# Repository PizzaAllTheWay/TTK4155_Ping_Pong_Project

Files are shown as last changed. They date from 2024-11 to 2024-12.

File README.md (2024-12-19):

# Ping Pong Project
A School project for subject TTK4155. The goal of the project is to teach students how to develop and design Embedded Systems

Lord Have mercy on us
Let the grind BEGIN!

# Demo Video
Demo Video (https://www.youtube.com/watch?v=QTJpXrNRjtw)

Raw link: https://www.youtube.com/watch?v=QTJpXrNRjtw

# PCB
Very cool, very clean, thank you Benjamin for making an awesome PCB <3

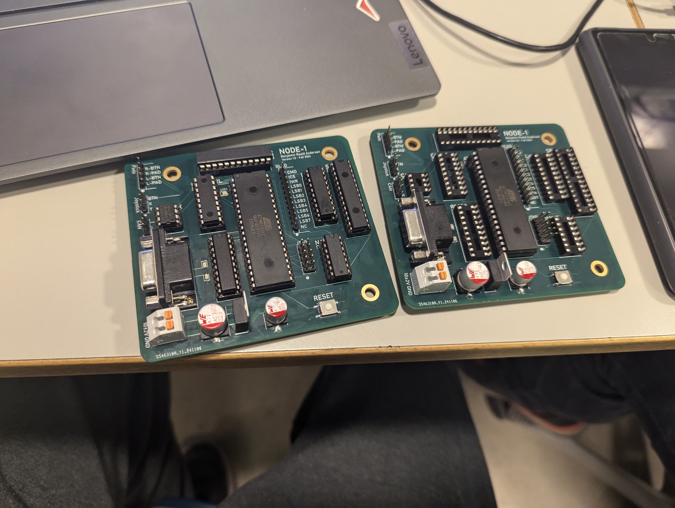
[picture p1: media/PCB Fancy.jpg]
PCB Fancy


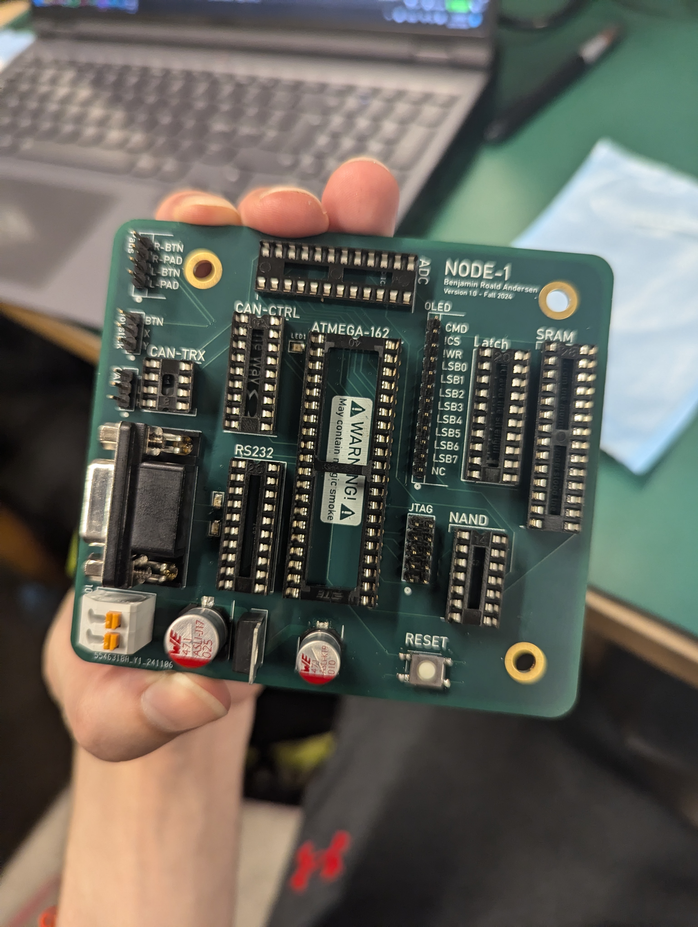
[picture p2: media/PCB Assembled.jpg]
PCB Assembled


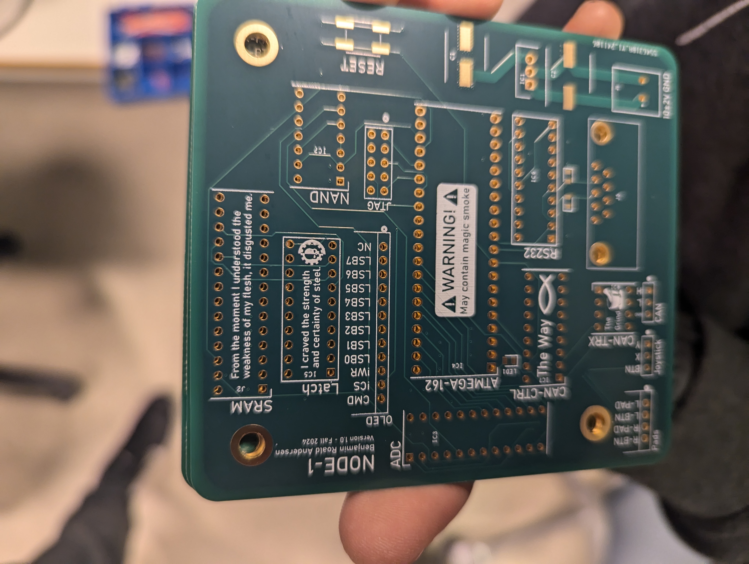
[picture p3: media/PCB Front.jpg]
PCB Front

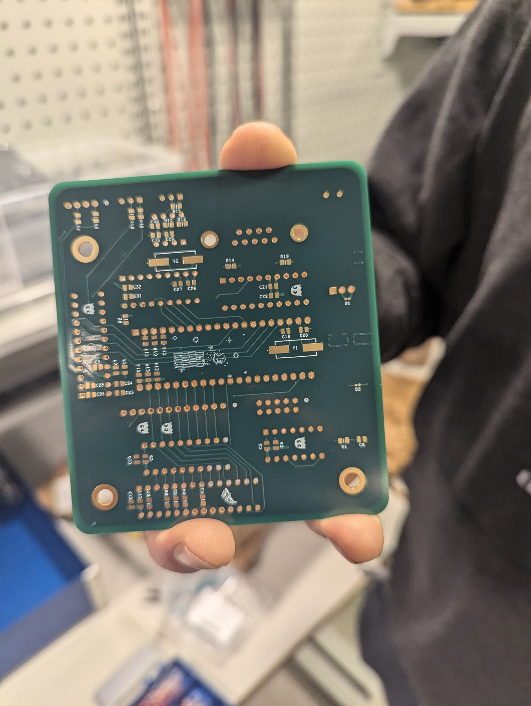
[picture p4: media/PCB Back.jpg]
PCB Back


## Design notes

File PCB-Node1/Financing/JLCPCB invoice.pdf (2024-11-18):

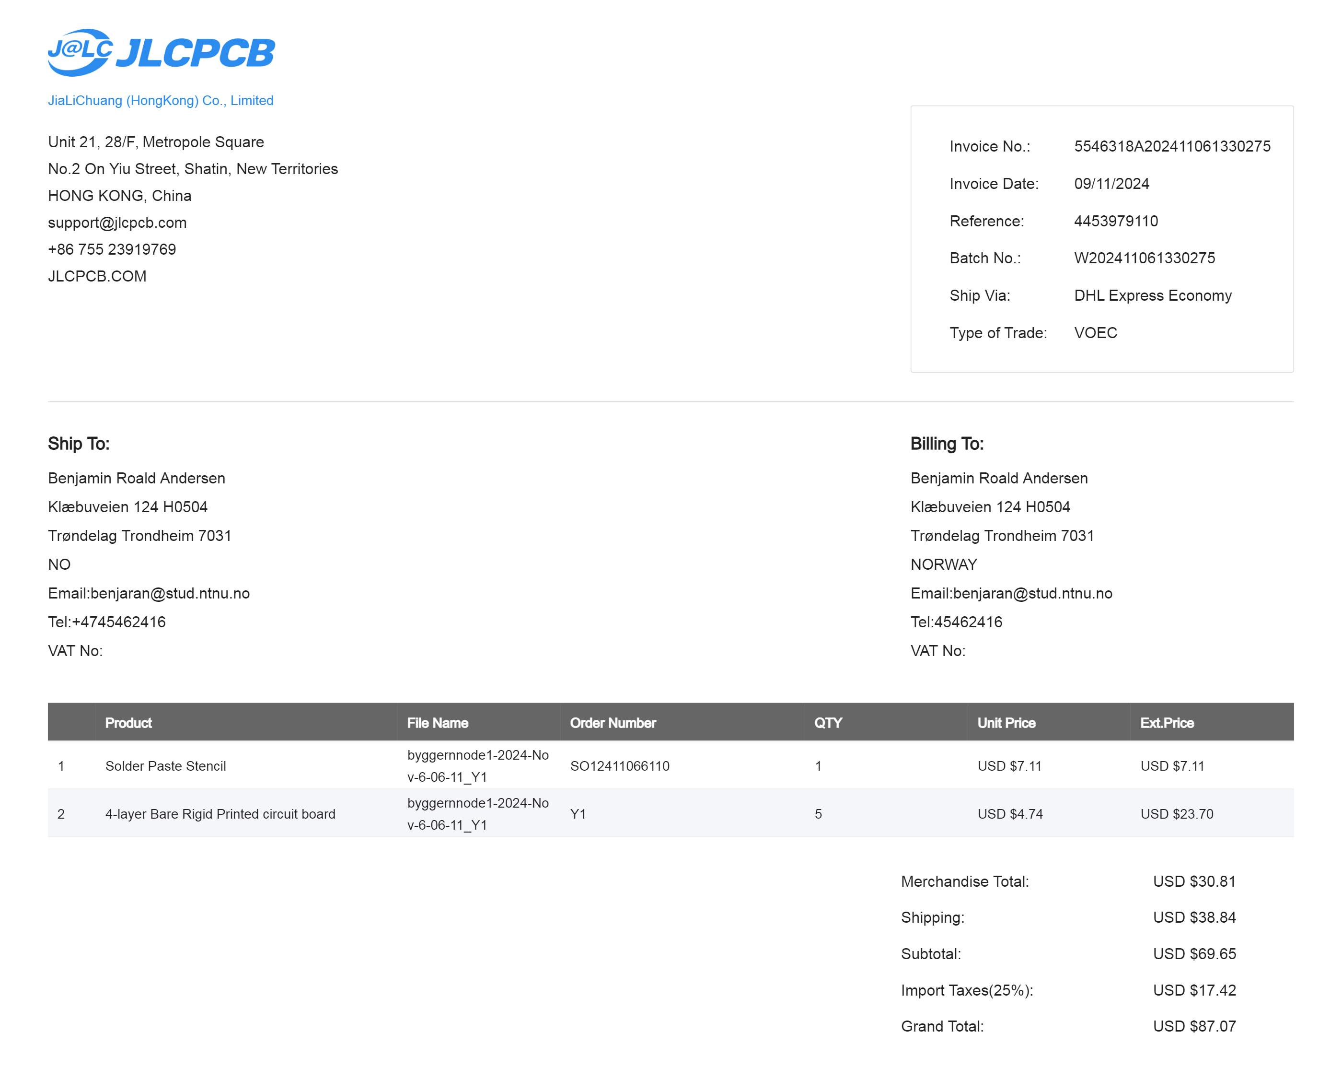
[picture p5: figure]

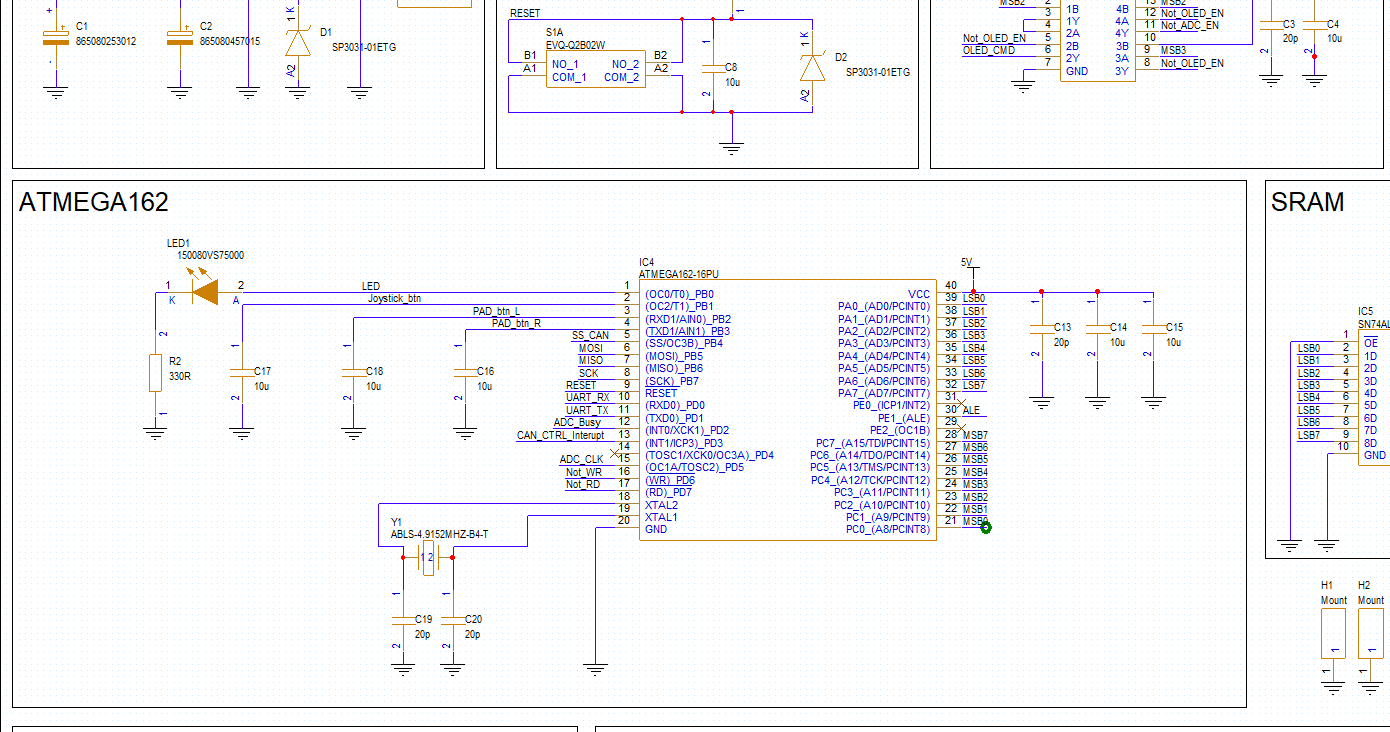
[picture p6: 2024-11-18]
PCB-Node1/Project/byggernnode1/BYGGERNNODE1.png

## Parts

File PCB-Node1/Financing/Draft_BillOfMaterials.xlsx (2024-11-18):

Connectors
3pinheader
amount per board | Capasitors | name | use | link | individual cost | Total cost
1 | 865080457015 | HV 470u | Filter | https://www.digikey.no/no/products/detail/w%C3%BCrth-elektronik/865080457015/5728038
1 | 865080253012 | 470u | Filter | https://www.digikey.no/no/products/detail/w%C3%BCrth-elektronik/865080253012/5728090
 | 885012107010 | 10u | decoupling | https://www.digikey.no/no/products/detail/w%C3%BCrth-elektronik/885012107010/5453475
2 | CC0805JRNPO9BN180 | 18p | OSC cap | https://www.digikey.no/no/products/detail/yageo/CC0805JRNPO9BN180/302836
2 | CC0805JRNPO9BN200 | 20p | OSC cap
 | 885012207098 | 100n | Filter | https://www.digikey.no/no/products/detail/w%C3%BCrth-elektronik/885012207098/5453935
 | Resistor
 | ERJ-6GEYJ103V | 10k |  | https://www.digikey.no/no/products/detail/panasonic-electronic-components/ERJ-6GEYJ103V/83062
 | ERJ-6GEYJ331V | 330R |  | https://www.digikey.no/no/products/detail/panasonic-electronic-components/ERJ-6GEYJ331V/89726
 | ERJ-6GEYJ202V | 2k |  | https://www.digikey.no/no/products/detail/panasonic-electronic-components/ERJ-6GEYJ202V/83028
 | Crystal
1 | ECS-160-20-5PX-TR |  | Can OSC | https://www.digikey.no/no/products/detail/ecs-inc/ECS-160-20-5PX-TR/765265
1 | ABLS-4.9152MHZ-B4-T |  | AT162 OSC | https://www.digikey.no/no/products/detail/abracon-llc/ABLS-4-9152MHZ-B4-T/2184149
 | LED
3 | 150080VS75000 | green LED | debug | https://www.digikey.no/no/products/detail/w%C3%BCrth-elektronik/150080VS75000/4489924
 | Button
1 | EVQ-Q2B02W |  |  | https://www.digikey.no/no/products/detail/panasonic-electronic-components/EVQ-Q2B02W/762881
 | Ssockets
1 | ED281DT |  | SRAM | https://www.digikey.no/no/products/detail/on-shore-technology-inc/ED281DT/4147600
1 | 1-2199299-5 |  | ATMEGA162 | https://www.digikey.no/no/products/detail/te-connectivity-amp-connectors/1-2199299-5/5022052
1 | DILB24P-224TLF |  | ADC | https://www.digikey.no/no/products/detail/amphenol-cs-fci/DILB24P-224TLF/5204412
1 | DILB14P-223TLF |  | NAND | https://www.digikey.no/no/products/detail/amphenol-cs-fci/DILB14P-223TLF/4292071
1 | DILB16P-223TLF |  | RS232 | https://www.digikey.no/no/products/detail/amphenol-cs-fci/DILB16P-223TLF/4292068
1 | DILB18P-223TLF |  | CAN ctrl | https://www.digikey.no/no/products/detail/amphenol-cs-fci/DILB18P-223TLF/5204410
1 | DILB8P-223TLF |  | CAN transceiver | https://www.digikey.no/no/products/detail/amphenol-cs-fci/DILB8P-223TLF/4292069
1 | DILB20P-223TLF |  | Adress latch | https://www.digikey.no/no/products/detail/amphenol-cs-fci/DILB20P-223TLF/4292067
 | 1 row Header pins
1 | 61302211121 |  | pinheader 1 row | https://www.digikey.no/no/products/detail/w%C3%BCrth-elektronik/61302211121/4846864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
 | 2 row header pins
1 | 61301021121 |  | Jtag 2 row | https://www.digikey.no/no/products/detail/w%C3%BCrth-elektronik/61301021121/2508441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

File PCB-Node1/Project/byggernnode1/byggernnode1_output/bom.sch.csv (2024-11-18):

Item Number | Quantity | Value | Description | Part Number | Part Reference | Manufacturer Name | Manufacturer Part Number | ID | SKU
1 | 1 | 865080253012 | Wurth Elektronik 470uF 10 V dc Aluminium Electrolytic Capacitor, WCAP-ASLI Series 2000h 8 (Dia.) x 10.35mm | 865080253012 | C1 | Würth Elektronik | 865080253012 | 440
2 | 1 | 865080457015 | Wurth Elektronik 470uF 25 V dc Aluminium Electrolytic Capacitor, WCAP-ASLI Series 2000h 10 (Dia.) x 10.35mm | 865080457015 | C2 | Würth Elektronik | 865080457015 | 437
3 | 1 | 20p | Multilayer Ceramic Chip Capacitor WCAP-CSGP Series 0805 10000000pF X5R0805106M010DFCT10000 | 885012107010 | C3 | Würth Elektronik | 885012107010 | 671
4 | 1 | 10u | Multilayer Ceramic Chip Capacitor WCAP-CSGP Series 0805 10000000pF X5R0805106M010DFCT10000 | 885012107010 | C4 | Würth Elektronik | 885012107010 | 674
5 | 1 | 10u | Multilayer Ceramic Chip Capacitor WCAP-CSGP Series 0805 10000000pF X5R0805106M010DFCT10000 | 885012107010 | C5 | Würth Elektronik | 885012107010 | 453
6 | 1 | 10u | Multilayer Ceramic Chip Capacitor WCAP-CSGP Series 0805 10000000pF X5R0805106M010DFCT10000 | 885012107010 | C6 | Würth Elektronik | 885012107010 | 456
7 | 1 | 20p | Multilayer Ceramic Chip Capacitor WCAP-CSGP Series 0805 10000000pF X5R0805106M010DFCT10000 | 885012107010 | C7 | Würth Elektronik | 885012107010 | 677
8 | 1 | 10u | Multilayer Ceramic Chip Capacitor WCAP-CSGP Series 0805 10000000pF X5R0805106M010DFCT10000 | 885012107010 | C8 | Würth Elektronik | 885012107010 | 521
9 | 1 | 20p | Multilayer Ceramic Chip Capacitor WCAP-CSGP Series 0805 10000000pF X5R0805106M010DFCT10000 | 885012107010 | C9 | Würth Elektronik | 885012107010 | 916
10 | 1 | 10u | Multilayer Ceramic Chip Capacitor WCAP-CSGP Series 0805 10000000pF X5R0805106M010DFCT10000 | 885012107010 | C10 | Würth Elektronik | 885012107010 | 919
11 | 1 | 20p | Multilayer Ceramic Chip Capacitor WCAP-CSGP Series 0805 10000000pF X5R0805106M010DFCT10000 | 885012107010 | C11 | Würth Elektronik | 885012107010 | 913
12 | 1 | 10u | Multilayer Ceramic Chip Capacitor WCAP-CSGP Series 0805 10000000pF X5R0805106M010DFCT10000 | 885012107010 | C12 | Würth Elektronik | 885012107010 | 910
13 | 1 | 20p | Multilayer Ceramic Chip Capacitor WCAP-CSGP Series 0805 10000000pF X5R0805106M010DFCT10000 | 885012107010 | C13 | Würth Elektronik | 885012107010 | 662
14 | 1 | 10u | Multilayer Ceramic Chip Capacitor WCAP-CSGP Series 0805 10000000pF X5R0805106M010DFCT10000 | 885012107010 | C14 | Würth Elektronik | 885012107010 | 665
15 | 1 | 10u | Multilayer Ceramic Chip Capacitor WCAP-CSGP Series 0805 10000000pF X5R0805106M010DFCT10000 | 885012107010 | C15 | Würth Elektronik | 885012107010 | 668
16 | 1 | 10u | Multilayer Ceramic Chip Capacitor WCAP-CSGP Series 0805 10000000pF X5R0805106M010DFCT10000 | 885012107010 | C16 | Würth Elektronik | 885012107010 | 450
17 | 1 | 10u | Multilayer Ceramic Chip Capacitor WCAP-CSGP Series 0805 10000000pF X5R0805106M010DFCT10000 | 885012107010 | C17 | Würth Elektronik | 885012107010 | 444
18 | 1 | 10u | Multilayer Ceramic Chip Capacitor WCAP-CSGP Series 0805 10000000pF X5R0805106M010DFCT10000 | 885012107010 | C18 | Würth Elektronik | 885012107010 | 447
19 | 1 | 20p | Multilayer Ceramic Chip Capacitor WCAP-CSGP Series 0805 10000000pF X5R0805106M010DFCT10000 | 885012107010 | C19 | Würth Elektronik | 885012107010 | 494
20 | 1 | 20p | Multilayer Ceramic Chip Capacitor WCAP-CSGP Series 0805 10000000pF X5R0805106M010DFCT10000 | 885012107010 | C20 | Würth Elektronik | 885012107010 | 491
21 | 1 | 20p | Multilayer Ceramic Chip Capacitor WCAP-CSGP Series 0805 10000000pF X5R0805106M010DFCT10000 | 885012107010 | C21 | Würth Elektronik | 885012107010 | 557
22 | 1 | 10u | Multilayer Ceramic Chip Capacitor WCAP-CSGP Series 0805 10000000pF X5R0805106M010DFCT10000 | 885012107010 | C22 | Würth Elektronik | 885012107010 | 553
23 | 1 | 100n | Multilayer Ceramic Chip Capacitor WCAP-CSGP Series 0805 10000000pF X5R0805106M010DFCT10000 | 885012107010 | C23 | Würth Elektronik | 885012107010 | 797
24 | 1 | 100n | Multilayer Ceramic Chip Capacitor WCAP-CSGP Series 0805 10000000pF X5R0805106M010DFCT10000 | 885012107010 | C24 | Würth Elektronik | 885012107010 | 801
25 | 1 | 10u | Multilayer Ceramic Chip Capacitor WCAP-CSGP Series 0805 10000000pF X5R0805106M010DFCT10000 | 885012107010 | C25 | Würth Elektronik | 885012107010 | 716
26 | 1 | 10u | Multilayer Ceramic Chip Capacitor WCAP-CSGP Series 0805 10000000pF X5R0805106M010DFCT10000 | 885012107010 | C26 | Würth Elektronik | 885012107010 | 713
27 | 1 | 20p | Multilayer Ceramic Chip Capacitor WCAP-CSGP Series 0805 10000000pF X5R0805106M010DFCT10000 | 885012107010 | C27 | Würth Elektronik | 885012107010 | 483
28 | 1 | 20p | Multilayer Ceramic Chip Capacitor WCAP-CSGP Series 0805 10000000pF X5R0805106M010DFCT10000 | 885012107010 | C28 | Würth Elektronik | 885012107010 | 486
29 | 1 | 20p | Multilayer Ceramic Chip Capacitor WCAP-CSGP Series 0805 10000000pF X5R0805106M010DFCT10000 | 885012107010 | C29 | Würth Elektronik | 885012107010 | 657
30 | 1 | 10u | Multilayer Ceramic Chip Capacitor WCAP-CSGP Series 0805 10000000pF X5R0805106M010DFCT10000 | 885012107010 | C30 | Würth Elektronik | 885012107010 | 654
31 | 1 | 20p | Multilayer Ceramic Chip Capacitor WCAP-CSGP Series 0805 10000000pF X5R0805106M010DFCT10000 | 885012107010 | C31 | Würth Elektronik | 885012107010 | 943
32 | 1 | 10u | Multilayer Ceramic Chip Capacitor WCAP-CSGP Series 0805 10000000pF X5R0805106M010DFCT10000 | 885012107010 | C32 | Würth Elektronik | 885012107010 | 940
33 | 1 | 10u | Multilayer Ceramic Chip Capacitor WCAP-CSGP Series 0805 10000000pF X5R0805106M010DFCT10000 | 885012107010 | C33 | Würth Elektronik | 885012107010 | 946
34 | 1 | CONN_003P_000C_1 |  | M20-9990345 | CAN_CONN1 | Harwin | M20-9990345 | 809
35 | 1 | SP3031-01ETG | ESD Suppressors / TVS Diodes 5V 1uA 10kV UNIDIRECTIONAL | SP3031-01ETG | D1 | LITTELFUSE | SP3031-01ETG | 1165
36 | 1 | SP3031-01ETG | ESD Suppressors / TVS Diodes 5V 1uA 10kV UNIDIRECTIONAL | SP3031-01ETG | D2 | LITTELFUSE | SP3031-01ETG | 1162
37 | 1 | Mount | Standoffs & Spacers WA-SMST SMT Steel 3.3mm Intrnl NonStop | 9774015960R | H1 | Würth Elektronik | 9774015960R | 949
38 | 1 | Mount | Standoffs & Spacers WA-SMST SMT Steel 3.3mm Intrnl NonStop | 9774015960R | H2 | Würth Elektronik | 9774015960R | 951
39 | 1 | Mount | Standoffs & Spacers WA-SMST SMT Steel 3.3mm Intrnl NonStop | 9774015960R | H3 | Würth Elektronik | 9774015960R | 953
40 | 1 | MC7805ACTG | 1A, 5V, Positive V Reg, MC7805ACTG MC7805ACTG, Voltage Regulator, 2.2A 5 V, +/-4%, 3-Pin TO-220 | MC7805ACTG | IC1 | onsemi | MC7805ACTG | 425
41 | 1 | SN74HC00N | Quad 2i/p NANDgate,SN74HC00N DIP14 25pcs | SN74HC00N | IC2 | Texas Instruments | SN74HC00N | 115
42 | 1 | MAX156BCNG+ | Analog to Digital Converters - ADC High-Speed, 8-Channel, 8-Bit ADC with Simultaneous Track/Holds and Reference | MAX156BCNG+ | IC3 | Analog Devices | MAX156BCNG+ | 86
43 | 1 | ATMEGA162-16PU | ATMEGA162-16PU, 8 bit AVR Microcontroller 16MHz 16 kB, 512 B Flash, 1 kB RAM, 40-Pin PDIP | ATMEGA162-16PU | IC4 | Microchip | ATMEGA162-16PU | 3
44 | 1 | SN74ALS573CN | Octal D-Type Transparent Latches With 3-State Outputs | SN74ALS573CN | IC5 | Texas Instruments | SN74ALS573CN | 65
45 | 1 | MAX233CPP+ | MAX233CPP+, Line Transceiver, EIA/TIA-232-E, RS-232, V.24, V.28 2-TX 2-RX 2-TRX, 5 V, 20-Pin PDIP | MAX233CPP+ | IC6 | Analog Devices | MAX233CPP+ | 1119
46 | 1 | MCP2515-I_P | Stand-Alone CAN Controller | MCP2515-I/P | IC7 | Microchip | MCP2515-I/P | 130
47 | 1 | MCP2551-I_P | High Speed CAN Transceiver,MCP2551-I/P Microchip MCP2551-I/P, CAN Transceiver 1-channel ISO 11898, 8-Pin PDIP | MCP2551-I/P | IC8 | Microchip | MCP2551-I/P | 149
48 | 1 | 691418320002 | WR-TBL Series 4183 - 3.81 mm 45° Cable Entry Screwless |  | J1 |  |  | 926
49 | 1 | ED281DT | 28 (2 x 14) Pos DIP, 0.3 (7.62mm) Row Spacing Socket Tin Through Hole" | ED281DT | J2 | On Shore Technology Inc. | ED281DT | 831
50 | 1 | 618009231121 | WURTH ELEKTRONIK - 618009231121 - SOCKET, D SUB, PCB, R/A, 9WAY | 618009231121 | J5 | Würth Elektronik | 618009231121 | 1147
51 | 1 | CONN_003P_000C_1 |  | M20-9990345 | JOYSTICK_CONN1 | Harwin | M20-9990345 | 685
52 | 1 | CONN_67997-210HLF |  | 67997-210HLF | JTAG_CONN1 | Amphenol ICC | 67997-210HLF | 748
53 | 1 | 150080VS75000 | Wurth Elektronik WL-SMCW 570 nm Green LED, 2012 (0805) Clear SMD package | 150080VS75000 | LED1 | Würth Elektronik | 150080VS75000 | 516
54 | 1 | 150080VS75000 | Wurth Elektronik WL-SMCW 570 nm Green LED, 2012 (0805) Clear SMD package | 150080VS75000 | LED2 | Würth Elektronik | 150080VS75000 | 625
55 | 1 | 150080VS75000 | Wurth Elektronik WL-SMCW 570 nm Green LED, 2012 (0805) Clear SMD package | 150080VS75000 | LED3 | Würth Elektronik | 150080VS75000 | 628
56 | 1 | CONN_012P_000C_1 |  | 705430011 | OLED_CONN1 | Molex Connector Corporation | 705430011 | 719
57 | 1 | 10k | Panasonic ERJ6GE Series Thick Film Surface Mount Fixed Resistor 0805 Case 10k +/-5% 0.125W +/-200ppm/C | ERJ-6GEYJ103V | R1 | Panasonic | ERJ-6GEYJ103V | 524
58 | 1 | 330R | Panasonic ERJ6GE Series Thick Film Surface Mount Fixed Resistor 0805 Case 10k +/-5% 0.125W +/-200ppm/C | ERJ-6GEYJ103V | R2 | Panasonic | ERJ-6GEYJ103V | 505
59 | 1 | 10k | Panasonic ERJ6GE Series Thick Film Surface Mount Fixed Resistor 0805 Case 10k +/-5% 0.125W +/-200ppm/C | ERJ-6GEYJ103V | R3 | Panasonic | ERJ-6GEYJ103V | 889
60 | 1 | 10k | Panasonic ERJ6GE Series Thick Film Surface Mount Fixed Resistor 0805 Case 10k +/-5% 0.125W +/-200ppm/C | ERJ-6GEYJ103V | R4 | Panasonic | ERJ-6GEYJ103V | 895
61 | 1 | 10k | Panasonic ERJ6GE Series Thick Film Surface Mount Fixed Resistor 0805 Case 10k +/-5% 0.125W +/-200ppm/C | ERJ-6GEYJ103V | R5 | Panasonic | ERJ-6GEYJ103V | 898
62 | 1 | 10k | Panasonic ERJ6GE Series Thick Film Surface Mount Fixed Resistor 0805 Case 10k +/-5% 0.125W +/-200ppm/C | ERJ-6GEYJ103V | R6 | Panasonic | ERJ-6GEYJ103V | 901
63 | 1 | 10k | Panasonic ERJ6GE Series Thick Film Surface Mount Fixed Resistor 0805 Case 10k +/-5% 0.125W +/-200ppm/C | ERJ-6GEYJ103V | R7 | Panasonic | ERJ-6GEYJ103V | 923
64 | 1 | 2k | Panasonic ERJ6GE Series Thick Film Surface Mount Fixed Resistor 0805 Case 10k +/-5% 0.125W +/-200ppm/C | ERJ-6GEYJ103V | R8 | Panasonic | ERJ-6GEYJ103V | 789
65 | 1 | 2k | Panasonic ERJ6GE Series Thick Film Surface Mount Fixed Resistor 0805 Case 10k +/-5% 0.125W +/-200ppm/C | ERJ-6GEYJ103V | R9 | Panasonic | ERJ-6GEYJ103V | 792
66 | 1 | 330R | Panasonic ERJ6GE Series Thick Film Surface Mount Fixed Resistor 0805 Case 10k +/-5% 0.125W +/-200ppm/C | ERJ-6GEYJ103V | R10 | Panasonic | ERJ-6GEYJ103V | 695
67 | 1 | 330R | Panasonic ERJ6GE Series Thick Film Surface Mount Fixed Resistor 0805 Case 10k +/-5% 0.125W +/-200ppm/C | ERJ-6GEYJ103V | R11 | Panasonic | ERJ-6GEYJ103V | 692
68 | 1 | 10k | Panasonic ERJ6GE Series Thick Film Surface Mount Fixed Resistor 0805 Case 10k +/-5% 0.125W +/-200ppm/C | ERJ-6GEYJ103V | R12 | Panasonic | ERJ-6GEYJ103V | 649
69 | 1 | 330R | Panasonic ERJ6GE Series Thick Film Surface Mount Fixed Resistor 0805 Case 10k +/-5% 0.125W +/-200ppm/C | ERJ-6GEYJ103V | R13 | Panasonic | ERJ-6GEYJ103V | 631
70 | 1 | 330R | Panasonic ERJ6GE Series Thick Film Surface Mount Fixed Resistor 0805 Case 10k +/-5% 0.125W +/-200ppm/C | ERJ-6GEYJ103V | R14 | Panasonic | ERJ-6GEYJ103V | 636
71 | 1 | inf | Panasonic ERJ6GE Series Thick Film Surface Mount Fixed Resistor 0805 Case 10k +/-5% 0.125W +/-200ppm/C | ERJ-6GEYJ103V | R15 | Panasonic | ERJ-6GEYJ103V | 644
72 | 1 | 120R | Panasonic ERJ6GE Series Thick Film Surface Mount Fixed Resistor 0805 Case 10k +/-5% 0.125W +/-200ppm/C | ERJ-6GEYJ103V | R16 | Panasonic | ERJ-6GEYJ103V | 641
73 | 1 | EVQ-Q2B02W | White Button Tactile Switch, Single Pole Single Throw (SPST) 20 mA@ 15 V dc 0.7mm | EVQ-Q2B02W | S1 | Panasonic | EVQ-Q2B02W | 498
74 | 1 | CONN_004P_000C_1 |  | 705430038 | TOUCH_CONN1 | Molex Connector Corporation | 705430038 | 775
75 | 1 | ABLS-4.9152MHZ-B4-T | HC/49US (AT49) SMD LOW PROFILE CRYSTAL | ABLS-4.9152MHZ-B4-T | Y1 | ABRACON | ABLS-4.9152MHZ-B4-T | 464
76 | 1 | ECS-160-20-5PX-TR | 16 MHz +/-30ppm Crystal 20pF 40 Ohms HC-49/US | ECS-160-20-5PX-TR | Y2 | ECS | ECS-160-20-5PX-TR | 480

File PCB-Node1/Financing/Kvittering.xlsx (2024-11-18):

DIGIKEY |  |  | JLCPCB |  |  | PCB Assembly Total:
Subtotal | 981.88 | NOK | Merchandise Total: | 30.81 | $ USD | Digikey | 1227.35 | NOK
Shipping | 0 | NOK | Shipping: | 38.84 | $ USD | Privat | -51.45 | NOK
VAT | 245.47 | NOK | Subtotal: | 69.65 | $ USD | JLCPCB | 980.32 | NOK
Total | 1227.35 | NOK | Import Taxes(25%): | 17.42 | $ USD | TOTAL: | 2156.22 | NOK
 |  |  | Grand Total: | 87.07 | $ USD
Privat |  |  | Grand Total: | 980.32 | NOK
D2FC-F-7N(20M) | -12.44 |  |  |  |  | PCB Assembly cost distribution
D2FC-F-7N(60M) | -16.6 |  |  |  |  | Benjamin | 718.74 | NOK
EVQ-P0E07K | -12.12 |  |  |  |  | Martynas | 718.74 | NOK
Subtotal | -41.16 |  |  |  |  | Iril | 718.74 | NOK
VAT | -10.29
Total | -51.45

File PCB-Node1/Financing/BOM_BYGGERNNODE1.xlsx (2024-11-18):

Page1
Quantity | 2 PCB Qantity | 3 PCB Qantity | 1 Order Quantity | 2 Order Quantity | 3 Order Quantity | single cost | 10pc cost | 50pc cost | 3 Order cost | Part num | Link
2 | 4 | 6 | 2 | 4 | 6 | kr 12.81 |  |  | kr 76.86 | 61302211121 | https://www.digikey.no/en/products/detail/w%C3%BCrth-elektronik/61302211121/4846864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 | X
1 | 2 | 3 | 2 | 3 | 4 | kr 10.19 |  |  | kr 40.76 | 865080457015 | https://www.digikey.no/no/products/detail/w%C3%BCrth-elektronik/865080457015/5728038 | X
1 | 2 | 3 | 2 | 3 | 4 | kr 5.99 |  |  | kr 23.96 | 865080253012 | https://www.digikey.no/no/products/detail/w%C3%BCrth-elektronik/865080253012/5728090 | X
17 | 34 | 51 | 18 | 35 | 52 | kr 2.00 | kr 1.86 | kr 1.86 | kr 96.67 | 885012107010 | https://www.digikey.no/no/products/detail/w%C3%BCrth-elektronik/885012107010/5453475 | X
 | 0 | 0 | 0 | 0 | 0 |  |  |  | kr 0.00
 | 0 | 0 | 0 | 0 | 0 |  |  |  | kr 0.00
12 | 24 | 36 | 13 | 25 | 37 | kr 1.26 | kr 0.73 | kr 0.51 | kr 27.20 | CC0805JRNPO9BN200 | https://www.digikey.no/no/products/detail/yageo/CC0805JRNPO9BN200/5884040 | x
 | 0 | 0 | 0 | 0 | 0 |  |  |  | kr 0.00
2 | 4 | 6 | 3 | 5 | 7 | kr 1.05 | kr 0.83 | kr 0.83 | kr 7.35 | 885012207098 | https://www.digikey.no/en/products/detail/w%C3%BCrth-elektronik/885012207098/5453935 | x
1 | 2 | 3 | 1 | 2 | 3 | kr 11.55 |  |  | kr 34.65 | 1-2199299-5 | https://www.digikey.no/en/products/detail/te-connectivity-amp-connectors/1-2199299-5/5022052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 | X
1 | 2 | 3 | 1 | 2 | 3 | kr 5.78 |  |  | kr 17.34 | DILB20P-223TLF | https://www.digikey.no/en/products/detail/amphenol-cs-fci/DILB20P-223TLF/4292067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 | X
1 | 2 | 3 | 1 | 2 | 3 | kr 5.78 |  |  | kr 17.34 | DILB20P-223TLF | https://www.digikey.no/en/products/detail/amphenol-cs-fci/DILB20P-223TLF/4292067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 | X
1 | 2 | 3 | 1 | 2 | 3 | kr 5.88 |  |  | kr 17.64 | DILB24P-224TLF | https://www.digikey.no/en/products/detail/amphenol-cs-fci/DILB24P-224TLF/5204412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 | X
1 | 2 | 3 | 1 | 2 | 3 | kr 5.57 |  |  | kr 16.71 | DILB14P-223TLF | DILB14P-223TLF Amphenol ICC (FCI) | Kontakter, forbindelser | DigiKey | X
1 | 2 | 3 | 1 | 2 | 3 | kr 3.99 |  |  | kr 11.97 | DILB18P-223TLF | https://www.digikey.no/en/products/detail/amphenol-cs-fci/DILB18P-223TLF/5204410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 | X
1 | 2 | 3 | 1 | 2 | 3 | kr 3.26 |  |  | kr 9.78 | DILB8P-223TLF | https://www.digikey.no/en/products/detail/amphenol-cs-fci/DILB8P-223TLF/4292069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 | X
1 | 2 | 3 | 1 | 2 | 3 | kr 12.39 |  |  | kr 37.17 | MC7805ACTG | https://www.digikey.no/en/products/detail/onsemi/MC7805ACTG/1481210?s=N4IgTCBcDaILIGEDsAOADAVgIIICoHEQBdAXyA | X
1 | 2 | 3 | 1 | 2 | 3 | kr 11.55 |  |  | kr 34.65 | 61301021121 | https://www.digikey.no/en/products/detail/w%C3%BCrth-elektronik/61301021121/2508441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 | X
1 | 2 | 3 | 1 | 2 | 3 | kr 31.23 |  |  | kr 93.69 | 618009231121 | https://www.digikey.no/no/products/detail/w%C3%BCrth-elektronik/618009231121/10484687 | X
1 | 2 | 3 | 2 | 3 | 3 | kr 4.94 |  |  | kr 14.82 | ED281DT | https://www.digikey.no/en/products/detail/on-shore-technology-inc/ED281DT/4147600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 | X
3 | 6 | 9 | 4 | 7 | 10 | kr 1.89 | kr 1.89 | kr 1.85 | kr 18.90 | 150080VS75000 | https://www.digikey.no/en/products/detail/w%C3%BCrth-elektronik/150080VS75000/4489924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 | X
0 | 0 | 0 | 0 | 0 | 0 |  |  |  | kr 0.00 | see item 1
5 | 10 | 15 | 6 | 11 | 16 | kr 1.05 | kr 0.41 | kr 0.26 | kr 6.56 | ERJ-6GEYJ331V | https://www.digikey.no/en/products/detail/panasonic-electronic-components/ERJ-6GEYJ331V/89726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 | X
7 | 14 | 21 | 8 | 15 | 22 | kr 1.05 | kr 0.41 | kr 0.26 | kr 9.02 | ERJ-6GEYJ103V | https://www.digikey.no/en/products/detail/panasonic-electronic-components/ERJ-6GEYJ103V/83062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 | X
 | 0 | 0 | 0 | 0 | 0 |  |  |  | kr 0.00
2 | 4 | 6 | 3 | 5 | 7 | kr 1.16 | kr 0.55 |  | kr 8.12 | ERJ-6ENF1200V | https://www.digikey.no/no/products/detail/panasonic-electronic-components/ERJ-6ENF1200V/1746457 | X
0 | 0 | 0 | 0 | 0 | 0 |  |  |  | kr 0.00
2 | 4 | 6 | 3 | 5 | 7 | kr 1.05 | kr 0.41 | kr 0.26 | kr 7.35 | ERJ-6GEYJ202V | https://www.digikey.no/en/products/detail/panasonic-electronic-components/ERJ-6GEYJ202V/83028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 | X
1 | 2 | 3 | 2 | 3 | 4 | kr 2.10 |  |  | kr 8.40 | EVQ-Q2B02W | https://www.digikey.no/en/products/detail/panasonic-electronic-components/EVQ-Q2B02W/762881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 | X
0 | 0 | 0 | 0 | 0 | 0 |  |  |  | kr 0.00 | see item 1
1 | 2 | 3 | 2 | 3 | 4 | kr 2.84 |  |  | kr 11.36 | ABLS-4.9152MHZ-B4-T | https://www.digikey.no/en/products/detail/abracon-llc/ABLS-4-9152MHZ-B4-T/2184149 | X
1 | 2 | 3 | 2 | 3 | 4 | kr 3.78 |  |  | kr 15.12 | ECS-160-20-5PX-TR | https://www.digikey.no/en/products/detail/ecs-inc/ECS-160-20-5PX-TR/765265 | X
2 | 4 | 6 | 3 | 5 | 7 | kr 2.18 | kr 1.50 |  | kr 15.26 | SP3031-01ETG | https://www.digikey.no/en/products/detail/littelfuse-inc/SP3031-01ETG/3598390 | X
1 | 2 | 3 | 1 | 2 | 3 | kr 12.60 |  |  | kr 37.80 | 691418320002 | https://www.digikey.no/en/products/detail/w%C3%BCrth-elektronik/691418320002/11477851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 | X
71 | 142 | 213 | 86 | 157 | 227 | All parts: |  |  | kr 716.44
 |  |  |  |  |  | Total: |  |  | kr 716.44
Privat:
1 |  | 2 |  |  | 2 | kr 5.99 |  |  | kr 11.98 |  | https://www.digikey.no/no/products/detail/omron-electronics-inc-emc-div/D2FC-F-7N-20M/20484121 | X
1 |  | 2 |  |  | 2 | kr 7.98 |  |  | kr 15.96 |  | https://www.digikey.no/no/products/detail/omron-electronics-inc-emc-div/D2FC-F-7N-60M/20484328 | X
1 |  | 3 |  |  | 3 | kr 3.89 |  |  | kr 11.67 |  | https://www.digikey.no/en/products/detail/panasonic-electronic-components/EVQ-P0E07K/286330 | X
 |  |  |  |  |  |  |  |  | kr 39.61

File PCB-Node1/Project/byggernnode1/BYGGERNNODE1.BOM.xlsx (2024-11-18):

Byggern 2024 Node 1 Revised: Monday, October 21, 2024
Benjamin Roald Andersen Revision: 1
Bill Of Materials October 22,2024 3:07:01 | Page1
Item | Quantity | 3 PCB Qantity | Order Quantity | Reference | Part | single cost | Minimum total cost | 3 Board cost | Order Cost (without quantity discount) | Part num | Link
______________________________________________ |  |  |  |  |  |  | 209.92
1 | 2 | 6 | 6 | Joystick_CONN,CAN_CONN | 3pin 1 row | 12.81 | 25.62 | 76.86 | 76.86 | 61302211121 | 61302211121 W黵th Elektronik | Kontakter, forbindelser | DigiKey
2 | 1 | 3 | 5 | C13 | 865080457015 | 10.19 | 10.19 | 30.57 | 50.95 | 865080457015 | https://www.digikey.no/no/products/detail/w%C3%BCrth-elektronik/865080457015/5728038
3 | 1 | 3 | 5 | C14 | 865080253012 | 5.99 | 5.99 | 17.97 | 29.95 | 865080253012 | https://www.digikey.no/no/products/detail/w%C3%BCrth-elektronik/865080253012/5728090
4 | 15 | 45 | 50 | C15,C16,C17,C18,C19,C24, | 10u | 2 | 30 | 90 | 100 | 885012107010 | https://www.digikey.no/no/products/detail/w%C3%BCrth-elektronik/885012107010/5453475
 |  | 0 |  | C25,C27,C30,C31,C33,C35, |  |  | 0 | 0 | 0
 |  | 0 |  | C36,C40,C42 |  |  | 0 | 0 | 0
5 | 11 | 33 | 50 | C20,C21,C22,C23,C26,C28, | 20p | 1.26 | 13.86 | 41.58 | 63 | CC0805JRNPO9BN200 | https://www.digikey.no/no/products/detail/yageo/CC0805JRNPO9BN200/5884040
 |  | 0 |  | C29,C32,C34,C39,C41 |  |  | 0 | 0 | 0
6 | 2 | 6 | 10 | C37,C38 | 100n | 1.05 | 2.1 | 6.3 | 10.5 | 885012207098 | 885012207098 W黵th Elektronik | Kondensatorer | DigiKey
7 | 1 | 3 | 4 | IC1 | ATMEGA162-16PU | 11.55 | 11.55 | 34.65 | 46.2 | 1-2199299-5 | 1-2199299-5 TE Connectivity AMP Connectors | Kontakter, forbindelser | DigiKey
8 | 1 | 3 | 4 | IC2 | MAX233CPP+ | 4.1 | 4.1 | 12.3 | 16.4 | DILB16P-223TLF | DILB16P-223TLF Amphenol ICC (FCI) | Kontakter, forbindelser | DigiKey
9 | 1 | 3 | 4 | IC3 | SN74ALS573CN | 5.78 | 5.78 | 17.34 | 23.12 | DILB20P-223TLF | DILB20P-223TLF Amphenol ICC (FCI) | Kontakter, forbindelser | DigiKey
10 | 1 | 3 | 4 | IC4 | MAX156BCNG+ | 5.88 | 5.88 | 17.64 | 23.52 | DILB24P-224TLF | DILB24P-224TLF Amphenol ICC (FCI) | Kontakter, forbindelser | DigiKey
11 | 1 | 3 | 4 | IC5 | SN74HC00N | 5.57 | 5.57 | 16.71 | 22.28 | DILB14P-223TLF | DILB14P-223TLF Amphenol ICC (FCI) | Kontakter, forbindelser | DigiKey
12 | 1 | 3 | 4 | IC6 | MCP2515-I_P | 3.99 | 3.99 | 11.97 | 15.96 | DILB18P-223TLF | DILB18P-223TLF Amphenol ICC (FCI) | Kontakter, forbindelser | DigiKey
13 | 1 | 3 | 4 | IC7 | MCP2551-I_P | 3.26 | 3.26 | 9.78 | 13.04 | DILB8P-223TLF | DILB8P-223TLF Amphenol ICC (FCI) | Kontakter, forbindelser | DigiKey
14 | 1 | 3 | 4 | IC8 | MC7805ACTG | 12.39 | 12.39 | 37.17 | 49.56 | MC7805ACTG | MC7805ACTG onsemi | Integrerte kretser (IC-er) | DigiKey
15 | 1 | 3 | 4 | JTAG_CONN | CONN_67997-210HLF | 11.55 | 11.55 | 34.65 | 46.2 | 61301021121 | 61301021121 W黵th Elektronik | Kontakter, forbindelser | DigiKey
16 | 1 | 3 | 4 | J2A | LD09S33E4GV00LF | 17.12 | 17.12 | 51.36 | 68.48 | LD09S33E4GV00LF | LD09S33E4GV00LF Amphenol ICC (FCI) | Kontakter, forbindelser | DigiKey
17 | 1 | 3 | 4 | J3 | ED281DT | 4.94 | 4.94 | 14.82 | 19.76 | ED281DT | ED281DT On Shore Technology Inc. | Kontakter, forbindelser | DigiKey
18 | 3 | 9 | 15 | LED1,LED2,LED3 | 150080VS75000 | 1.89 | 5.67 | 17.01 | 28.35 | 150080VS75000 | 150080VS75000 W黵th Elektronik | Optoelektronikk | DigiKey
19 | 1 | 3 | 0 | OLED_CONN | CONN_012P_000C_1 |  | 0 | 0 | 0 | see item 1
20 | 5 | 15 | 50 | R5,R6,R7,R9,R10 | 330R | 1.05 | 5.25 | 15.75 | 52.5 | ERJ-6GEYJ331V | ERJ-6GEYJ331V Panasonic Electronic Components | Motstander | DigiKey
21 | 7 | 21 | 50 | R8,R13,R16,R17,R18,R19, | 10k | 1.05 | 7.35 | 22.05 | 52.5 | ERJ-6GEYJ103V | ERJ-6GEYJ103V Panasonic Electronic Components | Motstander | DigiKey
 |  | 0 |  | R20 |  |  | 0 | 0 | 0
22 | 1 | 3 | 10 | R11 | 120R |  | 0 | 0 | 0 | ERJ-6ENF1200V | https://www.digikey.no/no/products/detail/panasonic-electronic-components/ERJ-6ENF1200V/1746457
23 | 1 | 3 | 0 | R12 | inf |  | 0 | 0 | 0
24 | 2 | 6 | 10 | R14,R15 | 2k | 1.05 | 2.1 | 6.3 | 10.5 | ERJ-6GEYJ202V | ERJ-6GEYJ202V Panasonic Electronic Components | Motstander | DigiKey
25 | 1 | 3 | 4 | S1A | EVQ-Q2B02W | 2.1 | 2.1 | 6.3 | 8.4 | EVQ-Q2B02W | EVQ-Q2B02W Panasonic Electronic Components | Brytere | DigiKey
26 | 1 | 3 | 0 | Touch_CONN | CONN_004P_000C_1 |  | 0 | 0 | 0 | see item 1
27 | 1 | 3 | 4 | Y1 | ABLS-4.9152MHZ-B4-T | 2.84 | 2.84 | 8.52 | 11.36 | ABLS-4.9152MHZ-B4-T | ABLS-4.9152MHZ-B4-T Abracon LLC | Krystaller, oscillatorer | DigiKey
28 | 1 | 3 | 4 | Y2 | ECS-160-20-5PX-TR | 3.78 | 3.78 | 11.34 | 15.12 | ECS-160-20-5PX-TR | ECS-160-20-5PX-TR ECS Inc. | Krystaller, oscillatorer | DigiKey
29 | 2 | 6 | 10 | Z1,Z2 | CUHZ5V6_H3F | 3.47 | 6.94 | 20.82 | 34.7 | CUHZ5V6,H3F | CUHZ5V6,H3F Toshiba Semiconductor and Storage | Kretsbeskyttelse | DigiKey
 | 69 | 207 |  |  |  | Total: | 209.92 | 629.76 | 889.21
 | Privat:
30 | 1 | 2 | 2 |  | D2FC-F-7N(20M) | 5.99 | 5.99 | 11.98 | 11.98 |  | https://www.digikey.no/no/products/detail/omron-electronics-inc-emc-div/D2FC-F-7N-20M/20484121
31 | 1 | 2 | 2 |  | D2FC-F-7N(60M) | 7.98 | 7.98 | 15.96 | 15.96 |  | https://www.digikey.no/no/products/detail/omron-electronics-inc-emc-div/D2FC-F-7N-60M/20484328
32 | 1 | 2 | 2 |  | 1825966-1 | 2.21 | 2.21 | 4.42 | 4.42 |  | https://www.digikey.no/en/products/detail/te-connectivity-alcoswitch-switches/1825966-1/1680318
33 | 1 | 2 | 2 |  | PTS636 SP43 SMTR LFS | 2.42 | 2.42 | 4.84 | 4.84 |  | https://www.digikey.no/en/products/detail/c-k/PTS636-SP43-SMTR-LFS/10071725
34 | 1 | 2 | 2 |  | R-667079 | 2.73 | 2.73 | 5.46 | 5.46 |  | https://www.digikey.no/en/products/detail/mitsumi-electric-company-ltd/R-667079/11591259
35 | 1 | 2 | 3 |  | MJTP1250 | 3.78 | 3.78 | 7.56 | 11.34 |  | https://www.digikey.no/en/products/detail/apem-inc/MJTP1250/1798038
36 | 1 | 2 | 2 |  | PTS636 SM43 SMTR LFS | 2.42 | 2.42 | 4.84 | 4.84 |  | https://www.digikey.no/en/products/detail/c-k/PTS636-SM43-SMTR-LFS/10071723

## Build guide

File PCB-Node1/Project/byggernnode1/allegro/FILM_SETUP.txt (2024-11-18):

axlFilmCreate( "temp" ?negative nil ?undefineLineWidth 0.0200 ?sequence 0 
	?rotation 0 ?xOffset 0.0000 ?yOffset 0.0000 ?shapeBoundingBox 0.2540 ?mirrored nil ?fullContact nil 
	?suppressUnconnectPads nil ?drawMissingPadApertures nil ?useApertureRotation nil 
	?suppressShapeFill t ?vectorBasedPad t ?drawHolesOnly nil 
	?domains '(ipc2581 pdf artwork visibility ) ?ipc2581 '() 
	?layers '())
axlFilmCreate( "Cutout" ?negative nil ?undefineLineWidth 0.1500 ?sequence 15 
	?rotation 0 ?xOffset 0.0000 ?yOffset 0.0000 ?shapeBoundingBox 2.5400 ?mirrored nil ?fullContact nil 
	?suppressUnconnectPads nil ?drawMissingPadApertures nil ?useApertureRotation nil 
	?suppressShapeFill nil ?vectorBasedPad t ?drawHolesOnly nil 
	?domains '(ipc2581 pdf artwork visibility ) ?ipc2581 '() 
	?layers '("BOARD GEOMETRY/CUTOUT" ))
axlFilmCreate( "Silkscreen_bot" ?negative nil ?undefineLineWidth 0.1500 ?sequence 14 
	?rotation 0 ?xOffset 0.0000 ?yOffset 0.0000 ?shapeBoundingBox 2.5400 ?mirrored nil ?fullContact nil 
	?suppressUnconnectPads nil ?drawMissingPadApertures nil ?useApertureRotation nil 
	?suppressShapeFill nil ?vectorBasedPad t ?drawHolesOnly nil 
	?domains '(ipc2581 pdf artwork visibility ) ?ipc2581 '() 
	?layers '("PACKAGE GEOMETRY/SILKSCREEN_BOTTOM" "BOARD GEOMETRY/SILKSCREEN_BOTTOM" "REF DES/SILKSCREEN_BOTTOM" ))
axlFilmCreate( "Silkscreen_top" ?negative nil ?undefineLineWidth 0.1500 ?sequence 13 
	?rotation 0 ?xOffset 0.0000 ?yOffset 0.0000 ?shapeBoundingBox 2.5400 ?mirrored nil ?fullContact nil 
	?suppressUnconnectPads nil ?drawMissingPadApertures nil ?useApertureRotation nil 
	?suppressShapeFill nil ?vectorBasedPad t ?drawHolesOnly nil 
	?domains '(ipc2581 pdf artwork visibility ) ?ipc2581 '() 
	?layers '("PACKAGE GEOMETRY/SILKSCREEN_TOP" "BOARD GEOMETRY/SILKSCREEN_TOP" "REF DES/SILKSCREEN_TOP" ))
axlFilmCreate( "Assembly_bot" ?negative nil ?undefineLineWidth 0.1500 ?sequence 12 
	?rotation 0 ?xOffset 0.0000 ?yOffset 0.0000 ?shapeBoundingBox 2.5400 ?mirrored nil ?fullContact nil 
	?suppressUnconnectPads nil ?drawMissingPadApertures nil ?useApertureRotation nil 
	?suppressShapeFill nil ?vectorBasedPad t ?drawHolesOnly nil 
	?domains '(ipc2581 pdf artwork visibility ) ?ipc2581 '() 
	?layers '("REF DES/ASSEMBLY_BOTTOM" "PACKAGE GEOMETRY/ASSEMBLY_BOTTOM" ))
axlFilmCreate( "Assembly_top" ?negative nil ?undefineLineWidth 0.1500 ?sequence 11 
	?rotation 0 ?xOffset 0.0000 ?yOffset 0.0000 ?shapeBoundingBox 2.5400 ?mirrored nil ?fullContact nil 
	?suppressUnconnectPads nil ?drawMissingPadApertures nil ?useApertureRotation nil 
	?suppressShapeFill nil ?vectorBasedPad t ?drawHolesOnly nil 
	?domains '(ipc2581 pdf artwork visibility ) ?ipc2581 '() 
	?layers '("REF DES/ASSEMBLY_TOP" "PACKAGE GEOMETRY/ASSEMBLY_TOP" ))
axlFilmCreate( "Solderpaste_bot" ?negative nil ?undefineLineWidth 0.1500 ?sequence 10 
	?rotation 0 ?xOffset 0.0000 ?yOffset 0.0000 ?shapeBoundingBox 2.5400 ?mirrored nil ?fullContact nil 
	?suppressUnconnectPads nil ?drawMissingPadApertures nil ?useApertureRotation nil 
	?suppressShapeFill nil ?vectorBasedPad t ?drawHolesOnly nil 
	?domains '(ipc2581 pdf artwork visibility ) ?ipc2581 '() 
	?layers '("PACKAGE GEOMETRY/PASTEMASK_BOTTOM" "PIN/PASTEMASK_BOTTOM" "VIA CLASS/PASTEMASK_BOTTOM" ))
axlFilmCreate( "Solderpaste_top" ?negative nil ?undefineLineWidth 0.1500 ?sequence 9 
	?rotation 0 ?xOffset 0.0000 ?yOffset 0.0000 ?shapeBoundingBox 2.5400 ?mirrored nil ?fullContact nil 
	?suppressUnconnectPads nil ?drawMissingPadApertures nil ?useApertureRotation nil 
	?suppressShapeFill nil ?vectorBasedPad t ?drawHolesOnly nil 
	?domains '(ipc2581 pdf artwork visibility ) ?ipc2581 '() 
	?layers '("PACKAGE GEOMETRY/PASTEMASK_TOP" "PIN/PASTEMASK_TOP" "VIA CLASS/PASTEMASK_TOP" ))
axlFilmCreate( "Soldermask_bot" ?negative nil ?undefineLineWidth 0.1500 ?sequence 8 
	?rotation 0 ?xOffset 0.0000 ?yOffset 0.0000 ?shapeBoundingBox 2.5400 ?mirrored nil ?fullContact nil 
	?suppressUnconnectPads nil ?drawMissingPadApertures nil ?useApertureRotation nil 
	?suppressShapeFill nil ?vectorBasedPad t ?drawHolesOnly nil 
	?domains '(ipc2581 pdf artwork visibility ) ?ipc2581 '() 
	?layers '("PACKAGE GEOMETRY/SOLDERMASK_BOTTOM" "BOARD GEOMETRY/SOLDERMASK_BOTTOM" "PIN/SOLDERMASK_BOTTOM" "VIA CLASS/SOLDERMASK_BOTTOM" ))
axlFilmCreate( "Soldermask_top" ?negative nil ?undefineLineWidth 0.1500 ?sequence 7 
	?rotation 0 ?xOffset 0.0000 ?yOffset 0.0000 ?shapeBoundingBox 2.5400 ?mirrored nil ?fullContact nil 
	?suppressUnconnectPads nil ?drawMissingPadApertures nil ?useApertureRotation nil 
	?suppressShapeFill nil ?vectorBasedPad t ?drawHolesOnly nil 
	?domains '(ipc2581 pdf artwork visibility ) ?ipc2581 '() 
	?layers '("PACKAGE GEOMETRY/SOLDERMASK_TOP" "BOARD GEOMETRY/SOLDERMASK_TOP" "PIN/SOLDERMASK_TOP" "VIA CLASS/SOLDERMASK_TOP" ))
axlFilmCreate( "Board_outline" ?negative nil ?undefineLineWidth 0.1500 ?sequence 6 
	?rotation 0 ?xOffset 0.0000 ?yOffset 0.0000 ?shapeBoundingBox 2.5400 ?mirrored nil ?fullContact nil 
	?suppressUnconnectPads nil ?drawMissingPadApertures nil ?useApertureRotation nil 
	?suppressShapeFill nil ?vectorBasedPad t ?drawHolesOnly nil 
	?domains '(ipc2581 pdf artwork visibility ) ?ipc2581 '() 
	?layers '("BOARD GEOMETRY/DESIGN_OUTLINE" ))
axlFilmCreate( "NCLEGEND-1-4" ?negative nil ?undefineLineWidth 0.1500 ?sequence 5 
	?rotation 0 ?xOffset 0.0000 ?yOffset 0.0000 ?shapeBoundingBox 2.5400 ?mirrored nil ?fullContact nil 
	?suppressUnconnectPads nil ?drawMissingPadApertures nil ?useApertureRotation nil 
	?suppressShapeFill nil ?vectorBasedPad t ?drawHolesOnly nil 
	?domains '(ipc2581 pdf artwork visibility ) ?ipc2581 '() 
	?layers '("MANUFACTURING/NCLEGEND-1-4" ))
axlFilmCreate( "4_BOTTOM" ?negative nil ?undefineLineWidth 0.1500 ?sequence 4 
	?rotation 0 ?xOffset 0.0000 ?yOffset 0.0000 ?shapeBoundingBox 2.5400 ?mirrored nil ?fullContact nil 
	?suppressUnconnectPads nil ?drawMissingPadApertures nil ?useApertureRotation nil 
	?suppressShapeFill nil ?vectorBasedPad t ?drawHolesOnly nil 
	?domains '(ipc2581 pdf artwork visibility ) ?ipc2581 '() 
	?layers '("VIA CLASS/BOTTOM" "PIN/BOTTOM" "ETCH/BOTTOM" ))
axlFilmCreate( "3_GND" ?negative nil ?undefineLineWidth 0.1500 ?sequence 3 
	?rotation 0 ?xOffset 0.0000 ?yOffset 0.0000 ?shapeBoundingBox 2.5400 ?mirrored nil ?fullContact nil 
	?suppressUnconnectPads nil ?drawMissingPadApertures nil ?useApertureRotation nil 
	?suppressShapeFill nil ?vectorBasedPad t ?drawHolesOnly nil 
	?domains '(ipc2581 pdf artwork visibility ) ?ipc2581 '() 
	?layers '("VIA CLASS/GND" "PIN/GND" "ETCH/GND" ))
axlFilmCreate( "2_LAYER_1" ?negative nil ?undefineLineWidth 0.1500 ?sequence 2 
	?rotation 0 ?xOffset 0.0000 ?yOffset 0.0000 ?shapeBoundingBox 2.5400 ?mirrored nil ?fullContact nil 
	?suppressUnconnectPads nil ?drawMissingPadApertures nil ?useApertureRotation nil 
	?suppressShapeFill nil ?vectorBasedPad t ?drawHolesOnly nil 
	?domains '(ipc2581 pdf artwork visibility ) ?ipc2581 '() 
	?layers '("VIA CLASS/LAYER_1" "PIN/LAYER_1" "ETCH/LAYER_1" ))
axlFilmCreate( "1_TOP" ?negative nil ?undefineLineWidth 0.1500 ?sequence 1 
	?rotation 0 ?xOffset 0.0000 ?yOffset 0.0000 ?shapeBoundingBox 2.5400 ?mirrored nil ?fullContact nil 
	?suppressUnconnectPads nil ?drawMissingPadApertures nil ?useApertureRotation nil 
	?suppressShapeFill nil ?vectorBasedPad t ?drawHolesOnly nil 
	?domains '(ipc2581 pdf artwork visibility ) ?ipc2581 '() 
	?layers '("VIA CLASS/TOP" "PIN/TOP" "ETCH/TOP" ))

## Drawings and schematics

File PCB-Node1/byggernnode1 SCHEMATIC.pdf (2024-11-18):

# Selector

Power Supply | Reset Switch

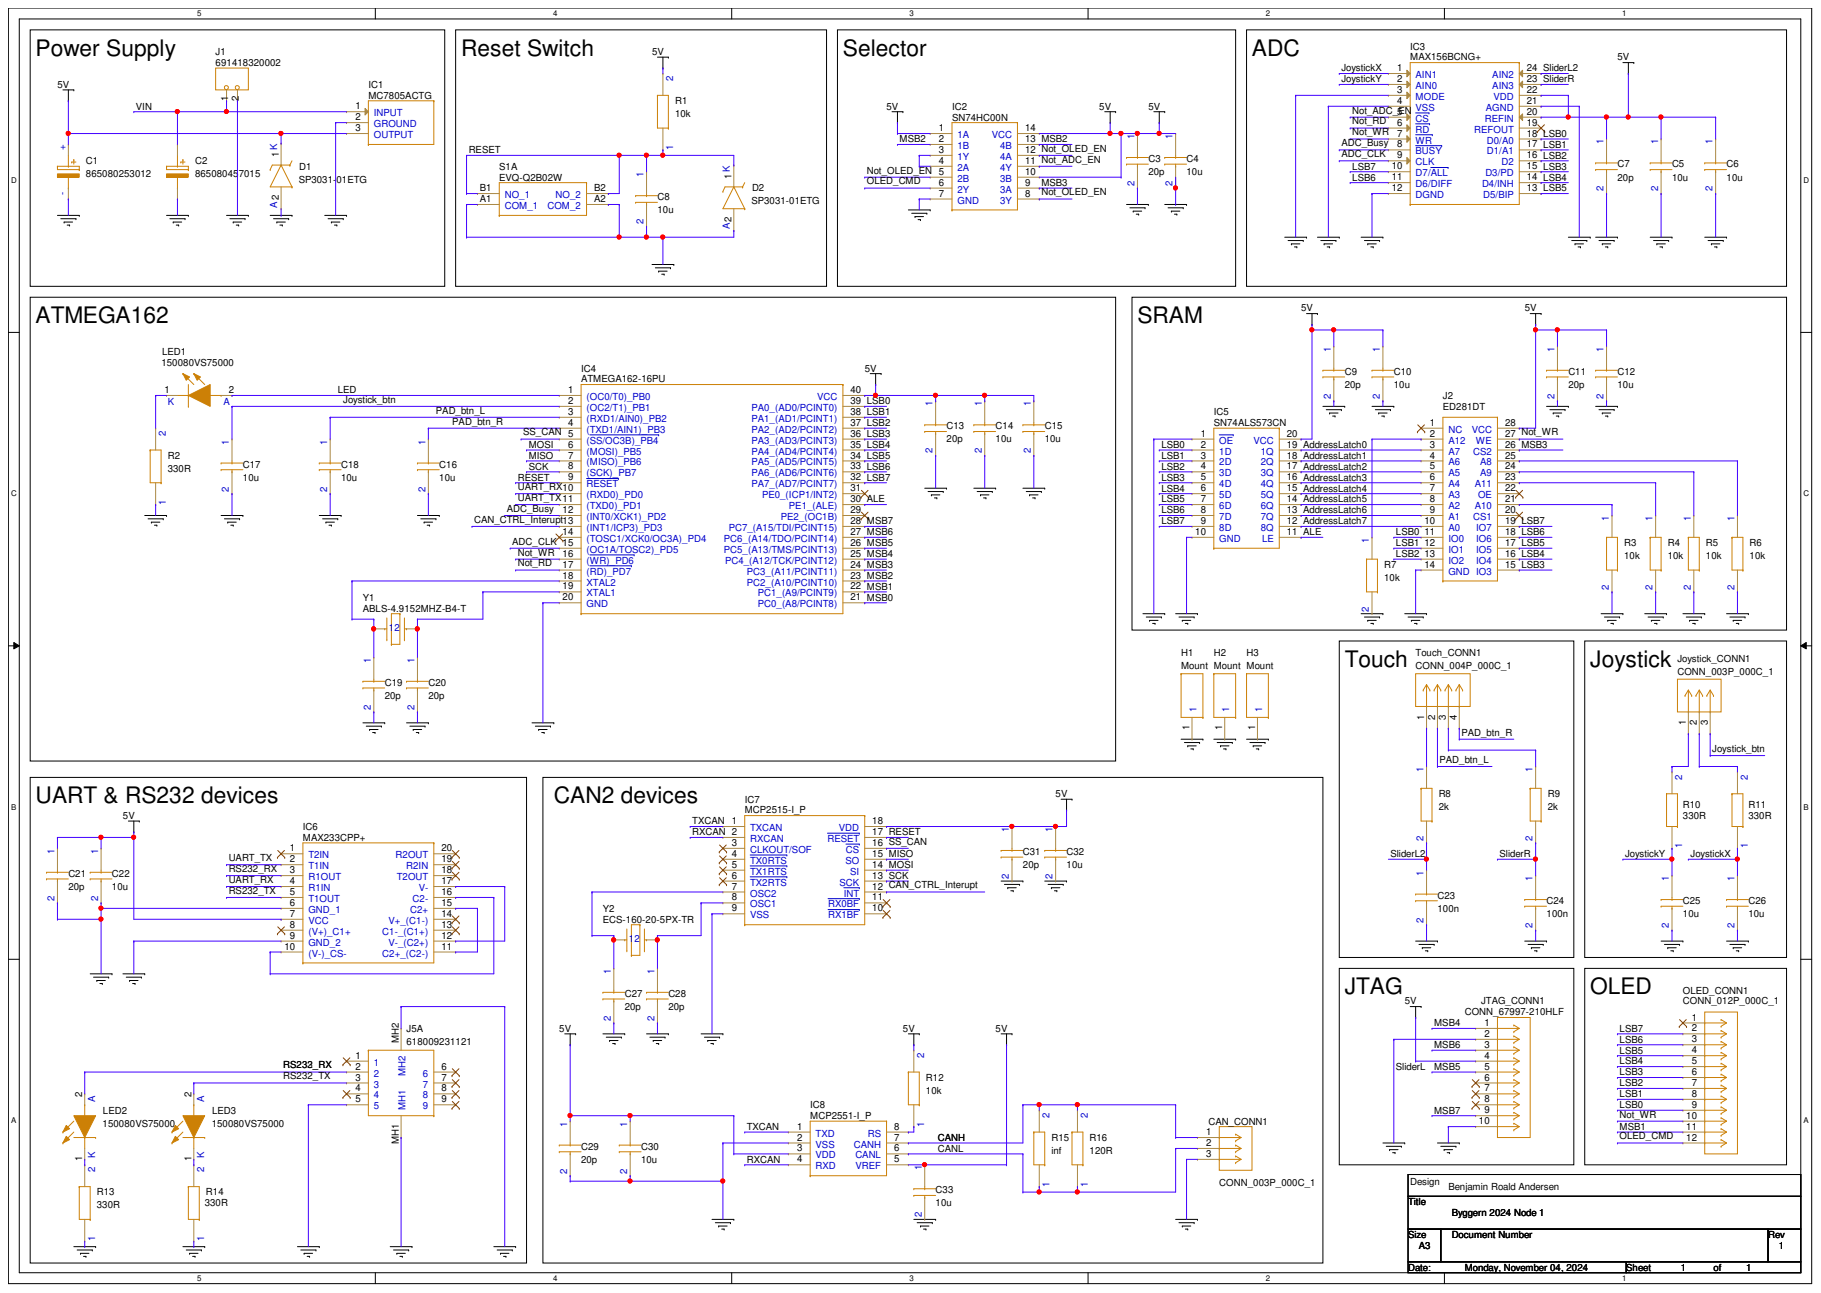
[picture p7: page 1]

Design Benjamin Roald Andersen

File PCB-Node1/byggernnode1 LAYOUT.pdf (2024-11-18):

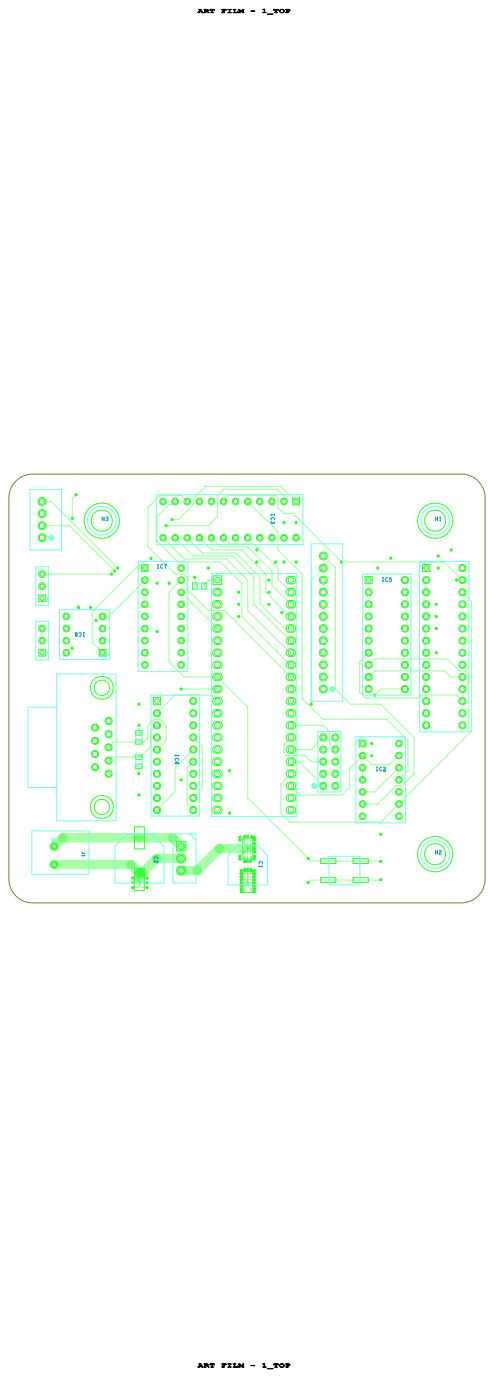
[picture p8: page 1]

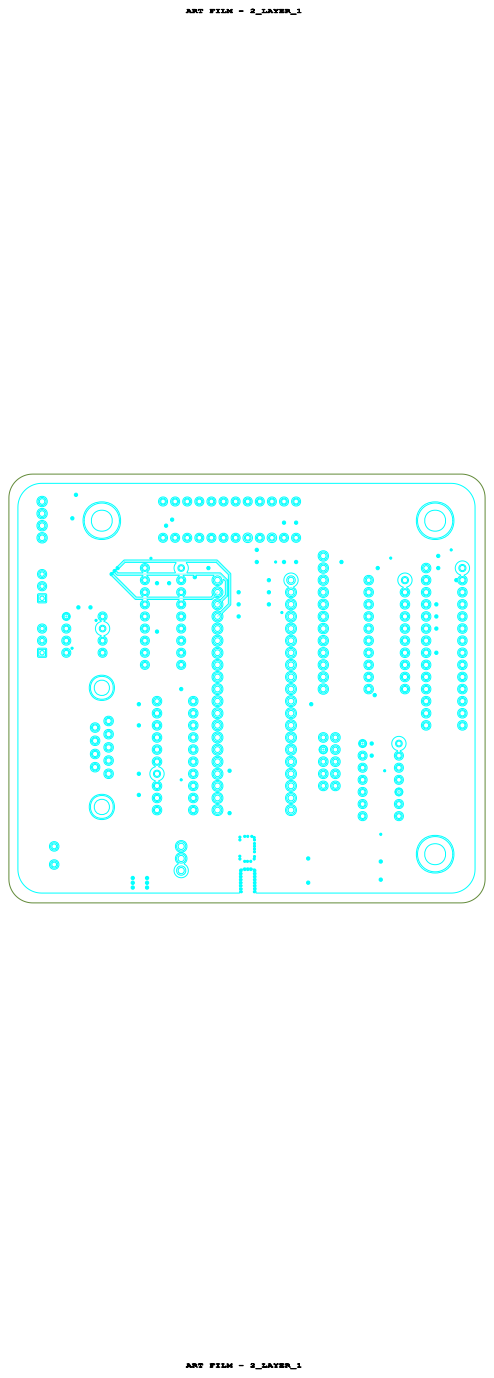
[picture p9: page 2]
ART FILM - 2_LAYER_1

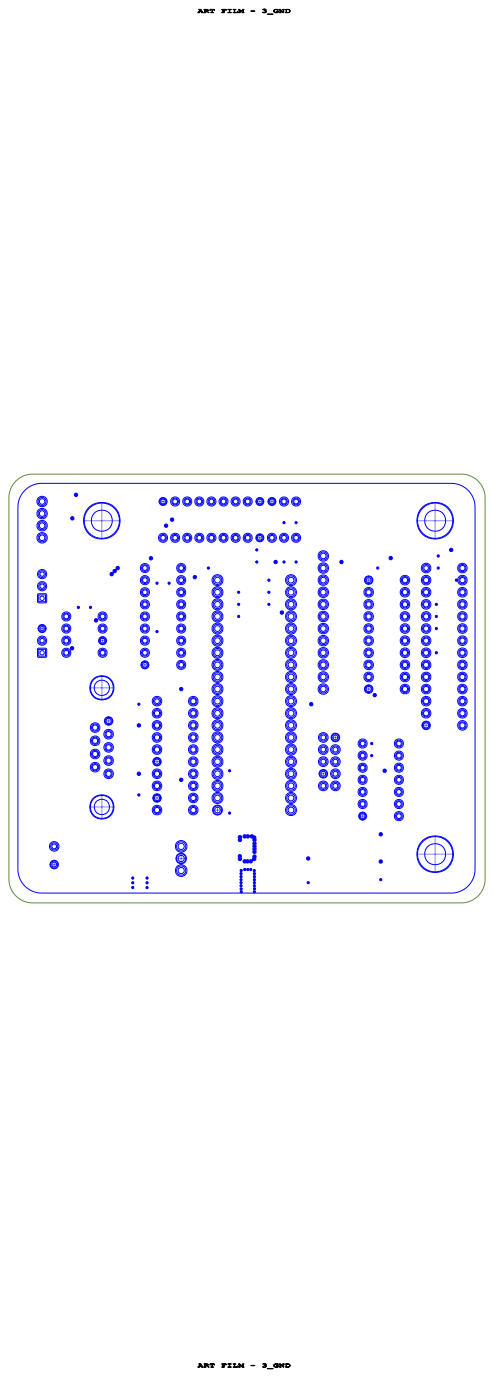
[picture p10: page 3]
ART FILM - 3_GND

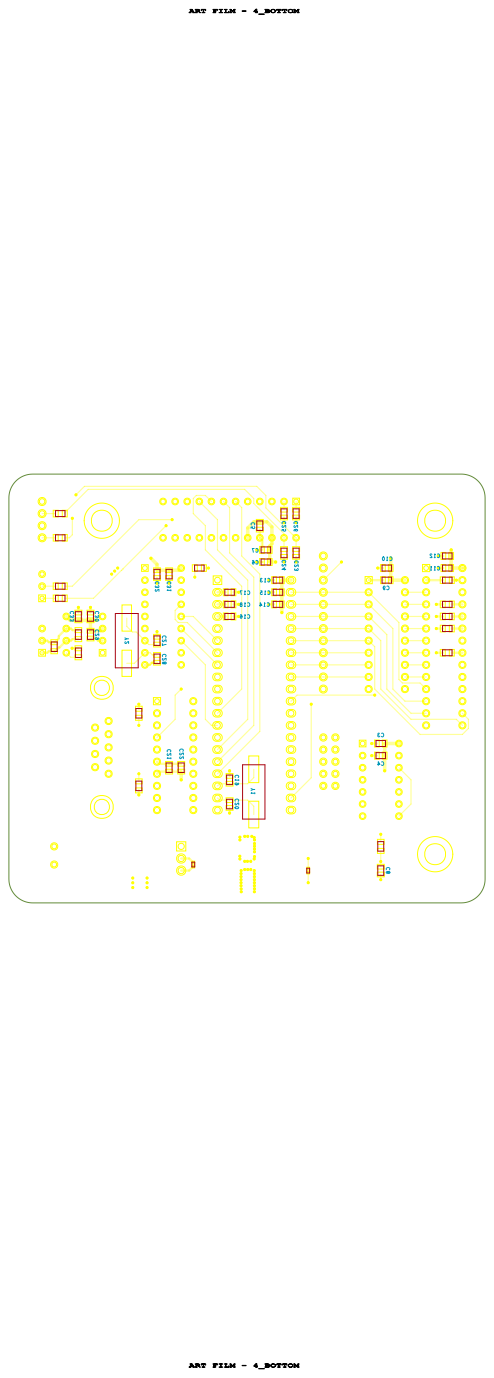
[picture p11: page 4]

# FIGURE FINISHED_SIZE

1.016

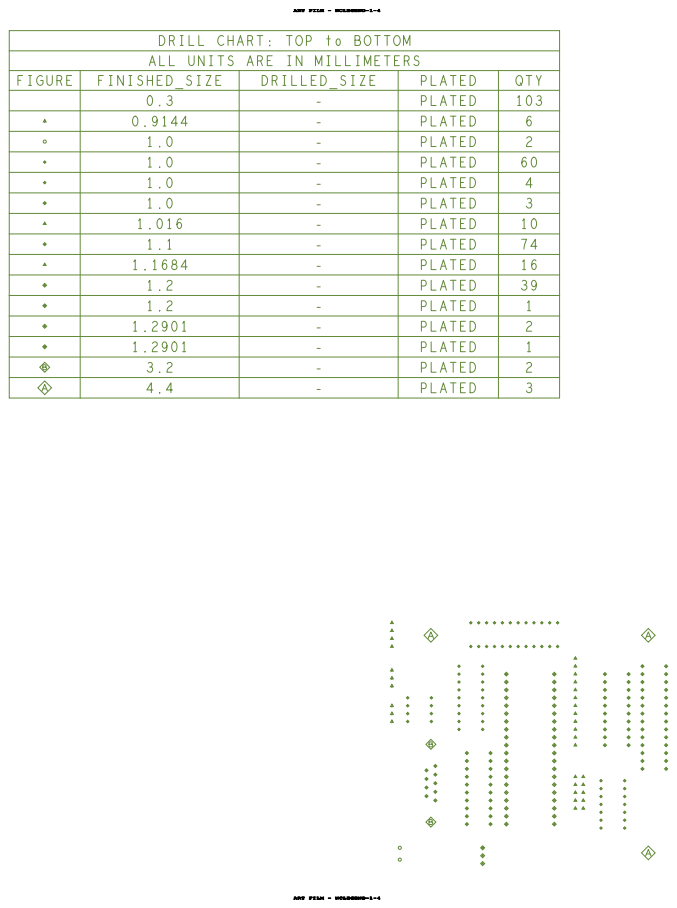
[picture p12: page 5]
DRILLED_SIZE; PLATED; QTY

ART FILM - NCLEGEND-1-4

DRILL CHART: TOP to BOTTOM
ALL UNITS ARE IN MILLIMETERS

ART FILM - Board_outline

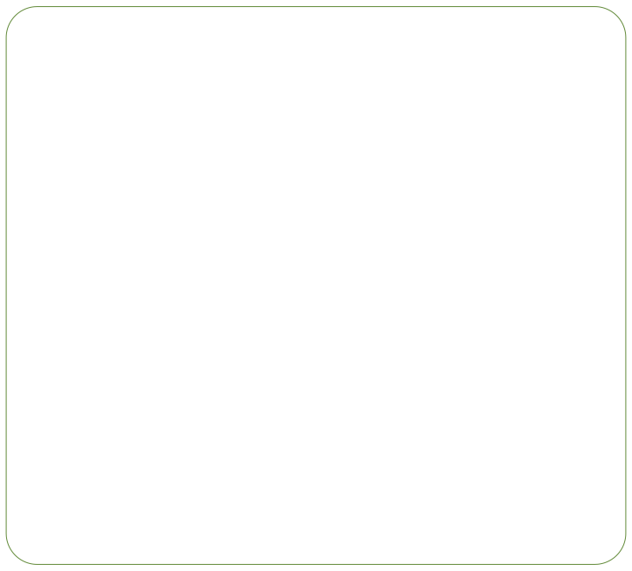
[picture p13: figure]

ART FILM - Board_outline

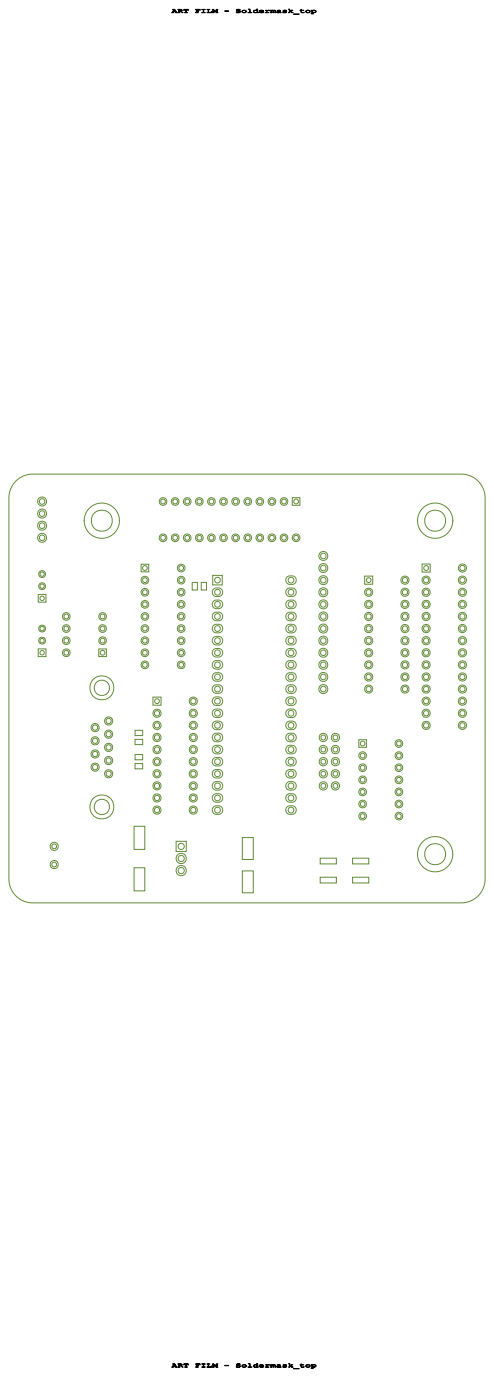
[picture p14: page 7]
ART FILM - Soldermask_top

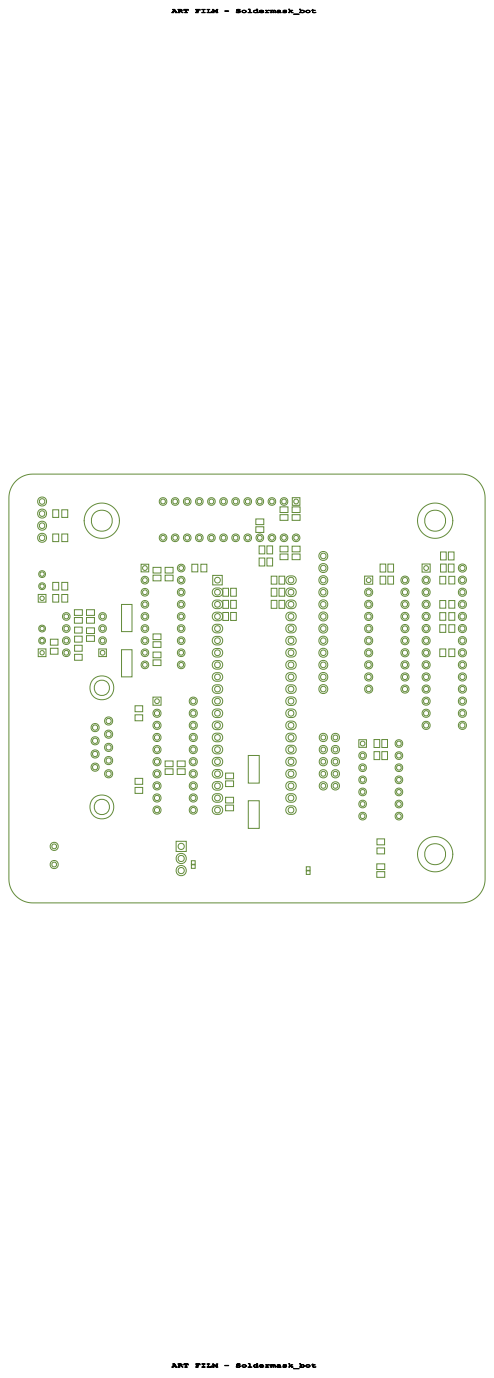
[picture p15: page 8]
ART FILM - Soldermask_bot

ART FILM - Solderpaste_top

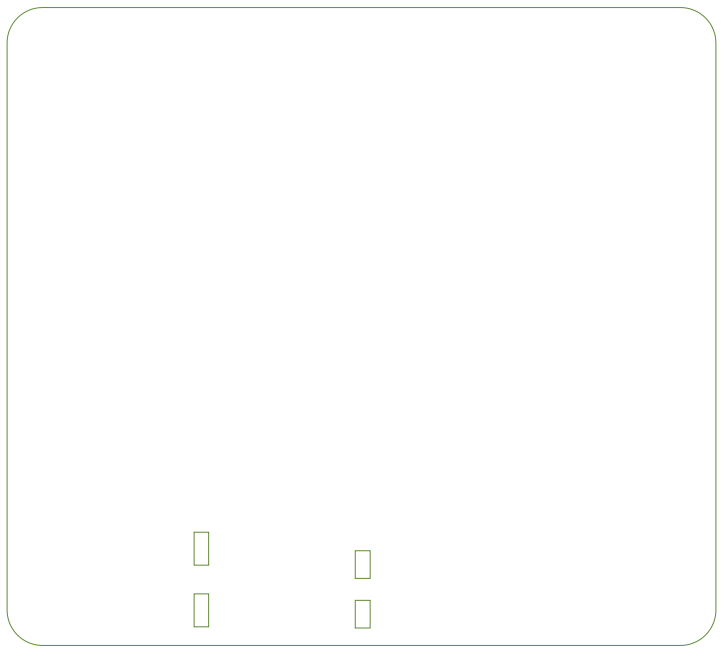
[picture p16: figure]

ART FILM - Solderpaste_top

ART FILM - Solderpaste_bot

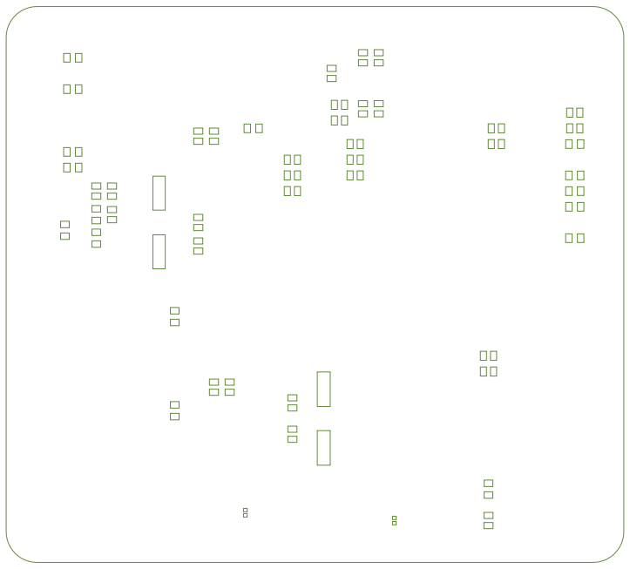
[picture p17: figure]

ART FILM - Solderpaste_bot

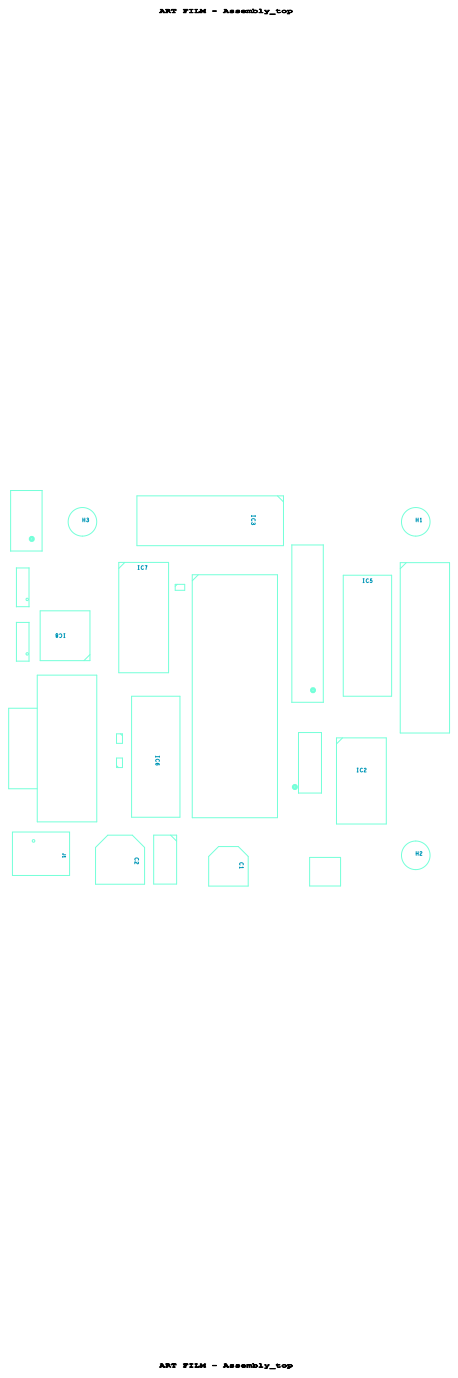
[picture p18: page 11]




ART FILM - Cutout

ART FILM - Cutout

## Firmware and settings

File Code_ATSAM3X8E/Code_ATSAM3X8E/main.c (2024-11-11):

/*
 * Code_ATSAM3X8E.c
 *
 * Created: 26/10/2024 14:43:32
 * Author : Martynas
 */ 



#define F_CPU 84000000UL // Set the CPU clock frequency 84 MHz



// Necessary Drivers for ATSAM3X8E Microcontrollers to work properly
#include "sam.h"
#include <stdio.h>
#include <stdint.h>



// Custom Drivers
#include "Drivers/Time/time.h"
#include "Drivers/Debugging/debug_led.h"
#include "Drivers/UART/uart_driver.h"
#include "Drivers/CAN/can.h"
#include "Drivers/Servo/servo_driver.h"
#include "Drivers/IR_LED/ir_led_driver.h"
#include "Drivers/Solenoid/solenoid_driver.h"
#include "Drivers/Motor/motor_driver.h"
#include "Drivers/Encoder/encoder_driver.h"
#include "Drivers/PID/pid_controller.h"



// Global Constant Variables
#define SOLENOID_BOUNCE_DURATION msecs(100)  // 100  [ms]
#define PID_UPDATE_INTERVAL      msecs(50)   // 50   [ms] TIPS: Should be the same as _MOTOR_UPDATE_INTERVAL
#define BALL_INTERVAL            msecs(5000) // 5000 [ms]
#define CAN_SEND_INTERVAL        msecs(1000) // 1000 [ms]
#define HEARTS_START_AMOUNT      5           // (Value MUST BE: 1 - 9) How many chances we have at the game before its GAME OVER X-X
#define HEARTS_RESET_KEY	     'R'		 // KEY value to reset heart



// Global Variables
uint8_t hearts = HEARTS_START_AMOUNT;

int8_t controls_joystick_y = 0;
int8_t controls_joystick_x = 0;
int8_t controls_pad_left = 0;
int8_t controls_pad_right = 0;
int8_t controls_joystick_button = 0;
int8_t controls_pad_left_button = 0;
int8_t controls_pad_right_button = 0;
char hearts_key = 0x00; // Responsible for reseting hearts (KEY: 'R' ie 0x52) other key values get ignored

uint8_t bounce_state = 0;

int8_t racket_speed = 0;



int main(void) {
	// Disable Watchdog Timer ----------
	WDT->WDT_MR = WDT_MR_WDDIS; // Set WDDIS bit to disable the watchdog timer
	
    // Initialize SAM system ----------
    SystemInit();
	
	// Initialize Debugging ----------
	debug_led_init();
	uart_init(84000000, 9600); // Initialize UART with CPU frequency (84 MHz) and desired baud rate (9600)
	
	// Setup Timers ----------
	// Variables to keep track of timers
	// SOLENOID:
	// For solenoid we add a timer just because we want a de-bounce effect
	// Basically timer is here to count until solenoid can retract
	//
	// PID:
	// There is no point in updating PID every clock cycle because of 3 reasons
	// PID doesn't get new reference and measured values each cycle (The processor is faster than peripheral interfaces)
	// PID controls Motors, witch itself has a strict limit and timer that doesn't allow it to update physically that fast
	// PID takes precious time to compute, no point in wasting time if it will give same result multiple times
	//
	// BALL:
	// The ping pong ball bounces, This can give false hearts subtractions
	// To mitigate this we have a small timer that starts counting after first heart got subtracted
	// Once the timer runs out only then can ping pong again have another heart subtraction if the ping pong is still there
	// 
	// CAN:
	// The CAN sending timings, as to not overwhelm the CAN buss and let us do other tasks at the same time
	// The Controls timings, as there is no point in sending data every microsecond
	uint64_t start_time_solenoid = 0;
	uint64_t start_time_pid = 0;
	uint64_t start_time_ball = 0;
	uint64_t start_time_can = 0;
	
	// Initialize CAN ----------
	// 500 kbps CAN Buss
	// CAN BIT TIMINGS:
	//	 - BRP = 83
	// 	 - PHASE1 = 6
	//   - PHASE2 = 6
	//   - PROP = 3
	//   - SJW = 1
	//   - SMP = 0
	// All of these timings MUST correspond to Node1 timings as well as adhere to ATSAM3X8E CAN Controller specifications
	// EXEPT for BRP! as BRP is the Baud Rate Prescaler
	// ATSAM3X8E CAN Controller specifications:
	//		- Bit Rate must be in standard TQ units (Time Quantum), and must be between 8-25 TQ
	//		- SJW must lie in 1 TQ range
	//		- PROP must be 1-8 TQ
	//		- PHASE1 must be 1-8 TQ
	//		- IPT <= PAHSE2 <= PHASE1
	//		- IPT (Information Processing Time) is fixed at 2 TQ and starts at the sample point
	//		- IPT represents the time needed by the CAN controller logic to process and determine the bit level (whether it’s a ‘1’ or ‘0’) at each sample point
	//		- SJW can only be set up to the minimum of PHASE1 or 4 TQ - whichever is smaller defines the maximum value that SJW can take.
	//
	// bit-rate we chose for node1 must be same for node2, ie 16 TQ (ie 500 kbps in our case)
	//		SJW + PROP + PHASE1 + PHASE2 = 16 TQ
	//
	// BRP is the value that gives identical TQ (Time Quantum) to the Node1 TQ
	// Even though Node1 (16 MHz) has different Frequency to Node2 (84 MHz)
	// Since we adjust BRP so that TQ stays the same
	// Then that means data rate on the buss will stay the same
	//
	// Solving for BRP:
	//		TQ = (1 + BRP)/MCK_REAL
	//			TQ: Time Quantum
	//			MCK_REAL: REAL Clock Speed
	//			BRP: Baud Rate Prescaling
	//		TQ * MCK_REAL = 1 + BRP
	//		BRP = TQ * MCK_REAL - 1
	//		MCK_REAL = MCK * prescale
	// MCK is the system clock speed and can be prescaled just like any other microcontroller
	// In ATSAM3X8E case, the peripherals on the high speed bridge are clocked by MCK
	// HOWEVER On the low-speed bridge, where CAN controller resides, MCK_REAL can be clocked at MCK divided by 2 or 4, this is to save power.
	// This division is set by PMC_PCR register as it is the Peripheral Control Register
	// By setting PMC_PCR we are setting a prescale for MCK_REAL, thus:
	//		prescale = 1/2
	// For more information about MCK (Master Clock), read ATSAM3X8E Data Sheet:
	// Page 39: 9.2 APB/AHB Bridge
	// Page 519 - 525: 27. Clock Generator
	// Page 526 - 566: 28. Power Management Controller (PMC)
	// Page 526: 28.2 Embedded Characteristics
	// Page 528 - 529: 28.7 Peripheral Clock Controller
	// Page 538: 28.15 Power Management Controller (PMC) User Interface
	// Page 566: 28.15.26 PMC Peripheral Control Register
	//		prescale = 1/2
	//		MCK_REAL = MCK * prescale
	//		MCK_REAL = MCK/2
	//		BRP = TQ * MCK_REAL - 1
	//		BRP = ((TQ * MCK)/2) - 1
	// We also have that TQ is time quantum
	//		TQ = 1/bit-rate
	//			bit-rate: data speed on the CAN buss we want
	//			n: Number of time quantums we have per data package sent/received
	//		TQ = 1/500 kbps
	//		BRP = ((TQ * MCK)/2) - 1
	//		BRP = (((1/500 kbps) * MCK)/2) - 1
	//			MCK (Master Clock): Just the external crystal oscillator for the ATSAM3X8E Microcontroller
	//		BRP = (((1/500 kbps) * 84 MHz)/2) - 1
	//		BRP = 83
	//
	// For more information about CAN Buss, read ATSAM3X8E Data Sheet:
	// Page 1185 - 1241: 40. Controller Area Network (CAN)
	// Page 1188 - 1199: 40.7 CAN Controller Features
	// Page 1192 - 1197: 40.7.4 CAN 2.0 Standard Features
	// Page 1192 - 1194: 40.7.4.1 CAN Bit Timing Configuration
	CanInit can_config = {
		.brp = 84,  // Baud Rate Prescaling (83)
		.phase1 = 6,
		.phase2 = 6,
		.propag = 3,
		.sjw = 1,
		.smp = 1
	}; // CAN initialization parameters
	can_init(can_config, 1); // Initialize CAN with the configuration and enable receive interrupts
	
	// Initialize Servo ----------
	servo_driver_init();
	
	// Initialize IR LED ----------
	ir_led_driver_init();
	
	// Initialize Solenoid ----------
	solenoid_driver_init();
	
	// Initialize Motor Control ----------
	int8_t kp = 10; // Proportional gain: reacts to current error (Recomended: 10)
	int8_t ki = 0; // Integral gain: reacts to accumulated error (Recomended: 0)
	int8_t kd = 0; // Derivative gain: reacts to error rate change (Recomended: 0)
	pid_controller_init(kp, ki, kd); // Initialize PID with gain values
	
	motor_driver_init(); // Motor Driver MUST ALWAYS be before Encoder Init!!! (Because Motor Driver resets the 0 point for the system by going to the edge of the box before encoder starts setting 0 point. Ensuring 0 point always stays on the left side of the box for optimal control)
	encoder_driver_init(); // ENcoder MUST come AFTER Motor Driver Init!!! (Because Motor Driver resets the 0 point for the system by going to the edge of the box before encoder starts setting 0 point. Ensuring 0 point always stays on the left side of the box for optimal control)
	
	
	
	// Infinite Loop
    while (1) {
		// Game (START) --------------------------------------------------
		// CAN Receive Logic ----------
		// Read CAN Buss
		CanMsg can_message_rx = can_get_latest_message();
		
		// Typecast all the messages into the correct format
		controls_joystick_y       = (int8_t)can_message_rx.byte[0];
		controls_joystick_x       = (int8_t)can_message_rx.byte[1];
		controls_pad_left         = (int8_t)can_message_rx.byte[2];
		controls_pad_right        = (int8_t)can_message_rx.byte[3];
		controls_joystick_button  = (int8_t)can_message_rx.byte[4];
		controls_pad_left_button  = (int8_t)can_message_rx.byte[5];
		controls_pad_right_button = (int8_t)can_message_rx.byte[6];
		hearts_key                =   (char)can_message_rx.byte[7];
		
		// Print all values
		//printf("Joystick Y: %d\n\r", controls_joystick_y);
		//printf("Joystick X: %d\n\r", controls_joystick_x);
		//printf("Pad Left: %d\n\r", controls_pad_left);
		//printf("Pad Right: %d\n\r", controls_pad_right);
		//printf("Joystick Button: %d\n\r", controls_joystick_button);
		//printf("Pad Left Button: %d\n\r", controls_pad_left_button);
		//printf("Pad Right Button: %d\n\r", controls_pad_right_button);
		//printf("Test Data: %c\n\r", test_data);
		
		// Solenoid Control ----------
		// 1. If button is not pressed, turn solenoid off and reset bounce_state.
		// 2. If button is pressed and bounce_state is 0, turn solenoid on, lock bounce_state, and start timer.
		// 3. If bounce duration has passed while holding the button on, turn solenoid off.
		if (controls_pad_right_button == 0) {
			solenoid_driver_off(); // OFF
			bounce_state = 0; // Reset
		}
		else if ((controls_pad_right_button == 1) && (bounce_state == 0)) {
			solenoid_driver_on(); // ON
			bounce_state = 1; // Lock
			start_time_solenoid = time_now(); // Start timer
		}
		else if ((bounce_state == 1) && ((time_now() - start_time_solenoid) > SOLENOID_BOUNCE_DURATION)) {
			solenoid_driver_off(); // OFF
		}
		
		// Angle Control ----------
		servo_driver_set_position(controls_joystick_x);
		
		// Position Control ----------
		// Calculate the optimal speed to get to our wanted position
		// Because PID takes time to calculate, updating it to many times has no physical benefits, therefore use time for something more productive until PID has a reason to be recalculated
		// Only update speed once PID timer has run out
		if ((time_now() - start_time_pid) > PID_UPDATE_INTERVAL) {
			// Reset timer
			start_time_pid = time_now();
			
			// Get wanted position
			int8_t racket_position_desired = controls_pad_right;
			
			// Get Ping-Pong Racket position
			int8_t racket_position = encoder_driver_get_position();
			
			// Calculate speed control
			racket_speed = pid_controller_get_u(racket_position_desired, racket_position);
			
			// Control Motor
			motor_driver_set_speed(racket_speed);
		}
		
		// Ball Detection ----------
		// Subtract hearts by 1 if the ball was detected AND if cool down period has passed
		if (ir_led_driver_get_status() != 0) {
			if ((time_now() - start_time_ball) >= BALL_INTERVAL) {
				hearts -= 1;

				// Reset the timer to start cool down
				start_time_ball = time_now();
			}
		}
		
		// Hearts Logic ----------
		// Check if enough time has passed since the last CAN message was sent
		if ((time_now() - start_time_can) >= CAN_SEND_INTERVAL) {
			// Reset the CAN start time for the next delay
			start_time_can = time_now();
			
			// Define the CAN message
			CanMsg can_message_tx;
			can_message_tx.id = CAN_ID_NODE2; // CAN ID
			can_message_tx.length = 8; // Message length
			can_message_tx.byte[0] = hearts; // Data bytes to send
			can_message_tx.byte[1] = hearts;
			can_message_tx.byte[2] = hearts;
			can_message_tx.byte[3] = hearts;
			can_message_tx.byte[4] = hearts;
			can_message_tx.byte[5] = hearts;
			can_message_tx.byte[6] = hearts;
			can_message_tx.byte[7] = hearts;
			
			// Send the message on the CAN bus
			can_tx(can_message_tx);
		}
		
		// Check if the reset hearts key was activated
		// If so reset the hearts
		if (hearts_key == HEARTS_RESET_KEY) hearts = HEARTS_START_AMOUNT;
		// Game (STOP) --------------------------------------------------
    }
}

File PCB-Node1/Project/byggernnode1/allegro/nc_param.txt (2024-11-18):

INTEGER-PLACES         3
DECIMAL-PLACES         5
X-OFFSET               0.000000
Y-OFFSET               0.000000
FEEDRATE               1
COORDINATES            ABSOLUTE
OUTPUT-UNITS           METRIC
TOOL-ORDER             INCREASING
REPEAT-CODES           NO
SUPPRESS-LEAD-ZEROES   NO
SUPPRESS-TRAIL-ZEROES  NO
SUPPRESS-EQUAL         NO
TOOL-SELECT            YES
OPTIMIZE_DRILLING      NO
ENHANCED_EXCELLON      YES
HEADER                 none
LEADER                 12
CODE                   ASCII
SEPARATE               YES
SEPARATE-ROUTING       YES
DRILLING               LAYER-PAIR
BACKDRILL              NO
COUNTER                NO
CAVITY                 NO
TOLERANCE_DRILL        YES
TOLERANCE_TRAVEL       YES
TOOL_SIZE              NO
ROTATION               YES
NON_STANDARD           YES
TOTAL_DRILL            NO
SEPARATE_SLOT          NO
SUPPRESS_TOLERANCE     YES
SUPPRESS_TOOLSIZE      YES
SUPPRESS_ROTATION      YES

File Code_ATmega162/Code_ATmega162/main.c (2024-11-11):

/*
 * Code_ATmega162.c
 *
 * Created: 26/08/2024 00:52:18
 * Author : Martynas
 */ 

#define F_CPU 4915200UL // Set the CPU clock frequency 4.9152 MHz



// Custom Libraries
#include "Drivers/Debugging/debug_led.h"
#include "Drivers/UART/uart_driver.h"
#include "Drivers/Time/time.h"
#include "Drivers/Controls/controls.h"
#include "Drivers/OLED/oled.h"
#include "Drivers/Menu/menu.h"
#include "Drivers/CAN/can_driver.h"




#include <avr/io.h>
#include <stdio.h>
#include <time.h>



// Global Constants
#define BAUD_RATE 9600

#define GAME_SCORE_INTERVAL 1000 // 100 [ms] How long it takes for the player to earn a score

#define CAN_ID_NODE1 1 // Our Node
#define CAN_ID_NODE2 2 // Motor Box Node

#define MENU_MAX 4 // 5 menus
#define POKEMON_MAX (11 - 1) // 11 Pokemon (start index 0, so subtract by 1)



// Global Variables
uint8_t score = 0x00;
uint8_t hearts = 0xFF;

int8_t joystic_y = 0;
int8_t button_L = 0;
int8_t button_R = 0;

int8_t menu_nr = 0;
int8_t bongocat_state = 0;
int8_t pokemon_state = 0;



int main(void)
{
	// Debugging Setup
	debug_led_init();
	uart_init(F_CPU, BAUD_RATE);
	time_init(F_CPU);

	// Interface Setup
	controls_init();
	menu_init();
	
	// CAN Setup
	//can_driver_init(MODE_LOOPBACK); // For Testing CAN
	can_driver_init(MODE_NORMAL);
	
	

    // Infinite loop
    while (1) {
		// Wait for input
		while (joystic_y == 0) {
			controls_refresh();
			joystic_y = controls_get_joystick_y();
			
			// Whilst waiting for input check if any of the buttons were pressed
			button_L = controls_get_pad_left_button();
			button_R = controls_get_pad_right_button();
			
			// Check witch menu we are inn to make the correct decision
			switch (menu_nr) {
				case 0:
					// Game (START) --------------------------------------------------
					// Ping Pong
					if (button_R == 1) {
						// Main Game Loop (START) --------------------------------------------------
						// Initialize Game Screen
						menu_pingpont_game(); // Set default screen
						menu_pingpont_set(score, hearts); // Set the score to default
						
						// Set up a timer for counting score
						unsigned long game_time = time_millis();
						
						// Start the game until you exit the game by pressing the left button
						// OR if you game_state = 1 (GAME OVER)
						uint8_t game_state = 0;
						while ((button_L == 0) && (game_state == 0)) {								
							// While no new messages are pending OR exit button not pressed, send controller data
							uint8_t can_message_available = 0;
							while ((!can_message_available) && (button_L == 0)) {
								// Get CAN message status 
								can_message_available = can_driver_message_available();
								
								// Get exit button status
								controls_refresh();
								button_L = controls_get_pad_left_button();

								// Declare CAN message type to format our message in
								can_message_t can_message_tx;

								// Set the CAN message ID
								can_message_tx.id = CAN_ID_NODE1;

								// Get Joystick Inputs
								// Set the message data to joystick inputs (8 bytes max)
								// Last byte just random as it is not used
								controls_refresh();
								can_message_tx.data[0] = controls_get_joystick_y();
								can_message_tx.data[1] = controls_get_joystick_x();
								can_message_tx.data[2] = controls_get_pad_left();
								can_message_tx.data[3] = controls_get_pad_right();
								can_message_tx.data[4] = controls_get_joystick_button();
								can_message_tx.data[5] = controls_get_pad_left_button();
								can_message_tx.data[6] = controls_get_pad_right_button();
								can_message_tx.data[7] = 'E';

								// Set the length of the message
								can_message_tx.length = 8;

								// Send the CAN message
								can_driver_send_message(&can_message_tx);
								
								// Increase players score if timer for that
								// A little treat :3 for surviving this long X)
								if ((time_millis() - game_time) > GAME_SCORE_INTERVAL) {
									// Update timer
									game_time = time_millis();
									
									// Increase score
									score++;
									
									// Update the screen with the new score
									menu_pingpont_set(score, hearts);
								}
							}
							
							// Once we get a pending message we read the message
							can_message_t can_message_rx;
							can_driver_read_message(&can_message_rx);

							// Check if the message is something we are interested in (ie from a sender ID we want to get data from and is not corrupted)
							if ((can_message_rx.id == CAN_ID_NODE2) && (can_message_rx.length == 8))  {
								// Recast the message type to the proper form
								uint8_t can_hearts = (uint8_t)can_message_rx.data[0];
								uint8_t test_data1 = (uint8_t)can_message_rx.data[1];
								uint8_t test_data2 = (uint8_t)can_message_rx.data[2];
								uint8_t test_data3 = (uint8_t)can_message_rx.data[3];
								uint8_t test_data4 = (uint8_t)can_message_rx.data[4];
								uint8_t test_data5 = (uint8_t)can_message_rx.data[5];
								uint8_t test_data6 = (uint8_t)can_message_rx.data[6];
								uint8_t test_data7 = (uint8_t)can_message_rx.data[7];
								
								// Check if the hearts we got from CAN buss is different from the hearts we stored
								// This is so that we don't update screen unnecessary
								if (hearts != can_hearts) {
									// Update hearts to the new CAN hearts
									hearts = can_hearts;
									
									// Update the screen with the new hearts
									menu_pingpont_set(score, hearts);
									
									// Check if the new hearts is not in range between 1 and 9
									// If so => GAME OVER
									if (hearts < 1 || hearts > 9) {
										game_state = 1; // GAME OVER
									}
								}
							}
							// Main Game Loop (STOP) --------------------------------------------------
						}
						
						// Reset Score ----------
						score = 0x00;
						
						// Reset Hearts ----------
						hearts = 0xFF;
						
						// Send Reset Can Message ----------
						// For the last time send CAN Message to reset motor box to its default state
						// Declare CAN message type to format our message in
						can_message_t can_message_tx;

						// Set the CAN message ID
						can_message_tx.id = CAN_ID_NODE1;

						// Send default Joystick Inputs
						// Set the message data to joystick inputs (8 bytes max)
						// Last byte just random as it is not used
						controls_refresh();
						can_message_tx.data[0] = 0;
						can_message_tx.data[1] = 0;
						can_message_tx.data[2] = 0;
						can_message_tx.data[3] = 0;
						can_message_tx.data[4] = 0;
						can_message_tx.data[5] = 0;
						can_message_tx.data[6] = 0;
						can_message_tx.data[7] = 'R'; // R => RESET HEARTS (Any other key will be ignored on NODE 2)

						// Set the length of the message
						can_message_tx.length = 8;
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

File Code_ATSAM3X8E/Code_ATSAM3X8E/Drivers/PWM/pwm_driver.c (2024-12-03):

/*
 * pwm_driver.c
 *
 * Created: 04/11/2024 11:43:23
 *  Author: Martynas
 */ 



#include "pwm_driver.h"



// Internal important values used in PWM Driver code
#define _SSC_WRITE_PROTECT_KEY 0x535343
#define _PWM_WRITE_PROTECT_KEY 0x50574D
#define _PMC_WRITE_PROTECT_KEY 0x504D43
#define _PWM_CLK_DIVA_FACTOR 84
#define _PWM_CHANNEL_MOTOR 0
#define _PWM_CHANNEL_SERVO 1



// Internal macros used inside this file disable
void _pwm_driver_disable() {
	// Disable PWM before configuring PWM registers
	// disable all 8 channels for PWM
	// Check and wait until all channels are disabled
	//
	// For more information about PWM registers, read ATSAM3X8E Data Sheet:
	// Page 970 - 1052: 38. Pulse Width Modulation (PWM)
	// Page 976 - 1002: 38.6 Functional Description
	// Page 1008: 38.7.3 PWM Disable Register
	// Page 1009: 38.7.4 PWM Status Register
	PWM->PWM_DIS =   PWM_DIS_CHID0
				   | PWM_DIS_CHID1
				   | PWM_DIS_CHID2
				   | PWM_DIS_CHID3
				   | PWM_DIS_CHID4
			       | PWM_DIS_CHID5
				   | PWM_DIS_CHID6
				   | PWM_DIS_CHID7;
	
	while (PWM->PWM_SR & ( PWM_SR_CHID0
						 | PWM_SR_CHID1
						 | PWM_SR_CHID2
						 | PWM_SR_CHID3
						 | PWM_SR_CHID4
						 | PWM_SR_CHID5
						 | PWM_SR_CHID6
						 | PWM_SR_CHID7)) {
		// Poll until CHID0-7 in PWM_SR are all 0 (indicating all channels are disabled)
	}
}

void _pwm_driver_enable() {
	// Enable PWM
	// Now that setup is done we can enable PWM signal again
	// We will enable only PWM channel 0 and 1, as that is the the only channel we are using
	// Because Pin PB12 and PB13 are connected to PWMH0 and PWMH1 (PWM Controller Channel 0 and 1)
	//
	// For more information about PWM_CPRDx and PWM_CDTYx, read ATSAM3X8E Data Sheet:
	// Page 977 - 992: 38.6.2 PWM Channel
	// Page 1007: 38.7.2 PWM Enable Register
	PWM->PWM_ENA =   PWM_ENA_CHID0
				   | PWM_ENA_CHID1;
}



// Setting up PWM for Motor Shield:
// DB12 (D20/SDA) (PWMH0) (Motor Control)
// PB13 (D21/SCL) (PWMH1) (Servo Control)
//
// For more information on Servo and Motor Controllers:
// Read: "TTK4155_Motor_Shield"
void pwm_driver_init() {
	// PIO Setup (START) --------------------------------------------------
	// Before Doing anything with PIO pins, we must enable write permissions to the registers
	// This will allow us to configure our PIO pins in special modes any way we like
	// Like for example setting PIO pins up for PWM mode
	// After disabling write locking we wait and check that the permissions are set as we want
	//
	// WPEN = 0 (Disables the Write Protect if WPKEY corresponds to 0x535343 (“SSC” in ASCII))
	// SSC_WRITE_PROTECT_KEY = 0x535343 (Idiot security to ensure the person who is writing to PWM signals has read the data sheet and understands the consequences of fucking up PWM registers, withouth this key no further PWM action can be made)
	//
	// For more information about write protection registers, read ATSAM3X8E Data Sheet:
	// Page 574 - 674: 30. Synchronous Serial Controller (SSC)
	// Page 616: 30.9.17 SSC Write Protect Mode Register
	// Page 617: 30.9.18 SSC Write Protect Status Register 
	uint8_t WPEN = 0;
	SSC->SSC_WPMR = (_SSC_WRITE_PROTECT_KEY << 8) // Set WPKEY
					| WPEN;                       // Set WPEN to disable pin write protect
	
	while (SSC->SSC_WPSR != 0) {
		// Poll until Write Protect Violation Status bit is 0
		// Also wait until bo Write Protect Violation Source emerge
		// (ie No Write Protect Violation has occurred)
	}
	
	// PIO Setup
	// Before using pins for PWM purposes we must configure PIO registers properly
	// We must specify the multiplexer mode for the pins to be in PWM mode
	// Since we are specifying the operation mode for multiplexer to be in PWM, we must also disable PIO registers
	// After disabling PIO registers we double check that and wait until PIO registers are disabled
	// Note that not all pins support PWM Controller mode
	// We have a shield connected to our Controller that has already predefined pins for our use cases
	// Servo PWM (Servo Control) and Enable PWM (Motor Control)
	// This means we have to choose specific pins for our operation:
	// We will be using PB12, witch connects to PWMH0 (PWM Controller channel 0) (Motor Control)
	// We will be using PB13, witch connects to PWMH1 (PWM Controller channel 1) (Servo Control)
	// NOTE: PB12 and PB13 is PWMH meaning HIGH. It is naturally at HIGH state unless pulse is sent
	//
	// For more information about PWM and PIO registers, read ATSAM3X8E Data Sheet:
	// Page 43: 9.3.3 PIO Controller C Multiplexing
	// Page 618 - 675: 31. Parallel Input/Output Controller (PIO)
	// Page 622: 31.5.2 I/O Line or Peripheral Function Selection
	// Page 622: 31.5.3 Peripheral A or B Selection
	// Page 623: 31.5.4 Output Control
	// Page 634: 31.7.2 PIO Controller PIO Disable Register
	// Page 635: 31.7.3 PIO Controller PIO Status Register
	// Page 656: 31.7.24 PIO Peripheral AB Select Register
	// Page 970 - 1052: 38. Pulse Width Modulation (PWM)
	PIOB->PIO_ABSR |= PIO_ABSR_P12; // Multiplex to peripheral function B for PIN12 (D20/SDA)
	PIOB->PIO_ABSR |= PIO_ABSR_P13; // Multiplex to peripheral function B for PIN13 (D21/SCL)
	PIOB->PIO_PDR |= PIO_PDR_P12; // Disable PIO from controlling PIN12 (D20/SDA)
	PIOB->PIO_PDR |= PIO_PDR_P13; // Disable PIO from controlling PIN13 (21/SCL)
	
	while ((PIOB->PIO_PSR & (PIO_PSR_P12 | PIO_PSR_P13)) != 0) {
		// Wait until PIO control is fully disabled for P12 and P13
		// Loop until PB12 and PB13 in PIO_PSR is 0, meaning:
		// PIO is inactive
		// BUT the peripheral is active (ie PWM peripheral for us)
	}
	// PIO Setup (STOP) --------------------------------------------------
	
	
	
	// PWM Setup (START) --------------------------------------------------
	// Before doing anything with PWM we must ensure WPSWSx and WPHWSx registers are cleared
	// This is to ensure we are able to write and read from PWM Registers
	// We write to WPCMD and WPRGx fields to disable write protections for PWM registers
	// This register has a key that is 0x50574D, by activating it we unlock the ability to write to all PWM registers
	// Then wait until all Write Protect SW and HW statuses are cleared
	//
	// bit 0 - 1: WPCMD = 0 (Disable the Write Protect SW of the register groups of which the bit WPRGx is at 1)
	// bit 2: WPRG0 = 1 (Enables WPCMD field setting to take effect on this WPRGx)
	// bit 3: WPRG1 = 1 (Enables WPCMD field setting to take effect on this WPRGx)
	// bit 4: WPRG2 = 1 (Enables WPCMD field setting to take effect on this WPRGx)
	// bit 5: WPRG3 = 1 (Enables WPCMD field setting to take effect on this WPRGx)
	// bit 6: WPRG4 = 1 (Enables WPCMD field setting to take effect on this WPRGx)
	// bit 7: WPRG5 = 1 (Enables WPCMD field setting to take effect on this WPRGx)
	// bit 8 - 31: WPKEY = 0x50574D (Idiot security to ensure the person who is writing to PWM signals has read the data sheet and understands the consequences of fucking up PWM registers, withouth this key no further PWM action can be made)
	//
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

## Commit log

2024-09-02 Uart sending working!, need receibving
2024-09-02 Debugging working properly with UART
2024-09-03 Updated driver code for later LAB2 usage :)
2024-09-05 Added external SRAM driver
2024-09-15 Added experimental ADC code
2024-09-16 ADC WORKSSSSS
2024-09-16 Added joystic, only joystic drift left
    [adc.c, controls.c, main.c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]
2024-09-21 ADC Done :)
2024-09-23 Added LP filter freq bode plt i.e. freq respons and phase
2024-09-23 fixed benjamin merge funky stuff
    [controls.c]
2024-09-28 fixed switch to use variable
2024-09-30 working ADC do not overwrite with garbage
2024-09-30 working OLED, menu, ADC, sprite, string
2024-10-07 Drivers in place, not tested
2024-10-14 made SPI send data
2024-10-19 added CAN driver, should test everything, doen't work yet
2024-10-21 SPI Finally working T_T
2024-10-21 Working CAN buss
2024-10-23 BOM missing some caps that were discovered during layout
    [BOM_BYGGERNNODE1.xlsx, Draft_BillOfMaterials.xlsx]
2024-10-23 Added large quantity pricing for relevant components, still missing some parts
    [BOM_BYGGERNNODE1.xlsx]
2024-10-23 Added all components and expanded on pricing
    [BOM_BYGGERNNODE1.xlsx]
2024-10-23 Added colors
    [BOM_BYGGERNNODE1.xlsx]
2024-10-23 Final cost optimisation by cutting margins on expensive components
    [BOM_BYGGERNNODE1.xlsx]
2024-10-26 Node 2 LED Blinking Working!!! :D
2024-10-26 Semi working CAN buss, now we need to adjust the timings X-X
2024-11-04 Start of PWM
2024-11-05 Servo done :)
2024-11-05 Kinda working ADC, not ideal tho
2024-11-05 ADC Done :D
2024-11-05 LAB IR and Servo DONE :DDD Tested and everything works good :)
2024-11-06 Added a propper timer logic in order to multitask CAN buss and other functionalities, not tested yet
2024-11-06 Tuned ADC to sample faster at 50 kHz isntead of 500 Hz. Needs testing
2024-11-06 remapped PWM pins to the motor shield pins
2024-11-09 CAN buss optimized UwU
2024-11-10 Solenoid and Encoder working :)
2024-11-11 Motor and PID done Everything works! :)
2024-11-11 Tuning PID
2024-11-18 Bill of materials
    [BOM_BYGGERNNODE1.xlsx, BYGGERNNODE1.BOM.xlsx]
2024-11-18 PCB design files
    [BYGGERNNODE1.DSN, OLD_byggernnode1.brd, art_param.txt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]
2024-11-18 design schematic and layout
